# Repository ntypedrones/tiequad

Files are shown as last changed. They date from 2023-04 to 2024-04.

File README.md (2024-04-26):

# TieQuad

TieQuad is a project aiming to produce a low cost, lightweight quadcopter frame, accepting that parts may break in a crash, but making sure that these breakable parts are easy to manufacture and replace. It is designed to accept standard 31.5mm square electronics stacks, and 16mm motor mounting.

The quadcopter frame consists of four hub peices and four motor mount peices, these are intended to be CNC cut from 1mm aluminium. These peices interface with two lengths of 8-10mm box section making up the arms, crossing at the centre.

The four hub peices need to be bent in two different ways: Two of the four need to be bent with the single tab on one side up and the two tabs on the other side down, and the other two hub peices need to be bent in the opposite manner. All motor mount tabs are to be bent in the same direction. All bends are to be 90 Degrees.

Cable ties hold the plates to the arms with friction, this means the arms require no complex manufacture at all, only cutting to length. Cable ties are to be placed over all the bent tabs, there are reliefs at the ends of the tabs to center them. The design was tested with 4mm wide cable ties.

Due to the asymetric design of the motor mounts, it is reccomended that the motor mounts are installed in a direction such that any stretching of the cable ties under load would cause the motor to change its thrust angle in a direction that would accentuate its gyroscopic effects on the system as a whole. i.e. for a standard quadcopter, the motor mount tabs should be on the left of the arm (when looking from the hub of the quadcopter), for clockwise spinning motors, and on the right of the arm for the anticlockwise motors.

There are extra peices available to reinforce the motor mounts and mitigate this effect for higher load applications. 8 will be required and they are to be bent and fitted under each motor mount cable tie. Half over the top of the existing mount, half contacting the bare side of the arm.

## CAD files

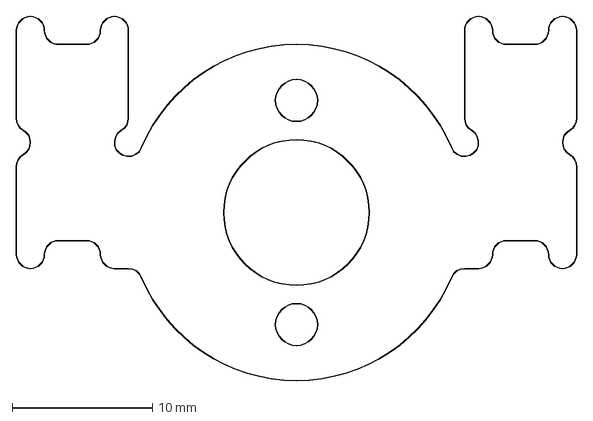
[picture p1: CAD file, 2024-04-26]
motor_mount.dxf
40.0 x 26.0 mm

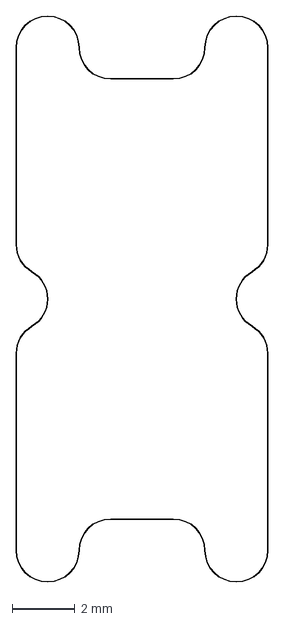
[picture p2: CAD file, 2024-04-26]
motor_mount_extra.dxf
8.00 x 18.0 mm

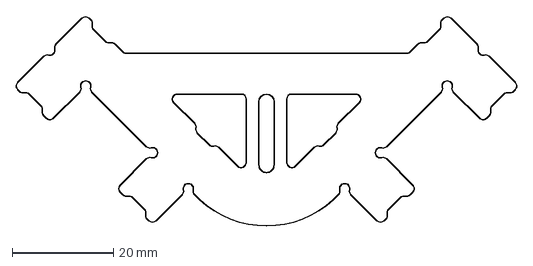
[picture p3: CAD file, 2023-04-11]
hub.dxf
98.7 x 41.4 mm
